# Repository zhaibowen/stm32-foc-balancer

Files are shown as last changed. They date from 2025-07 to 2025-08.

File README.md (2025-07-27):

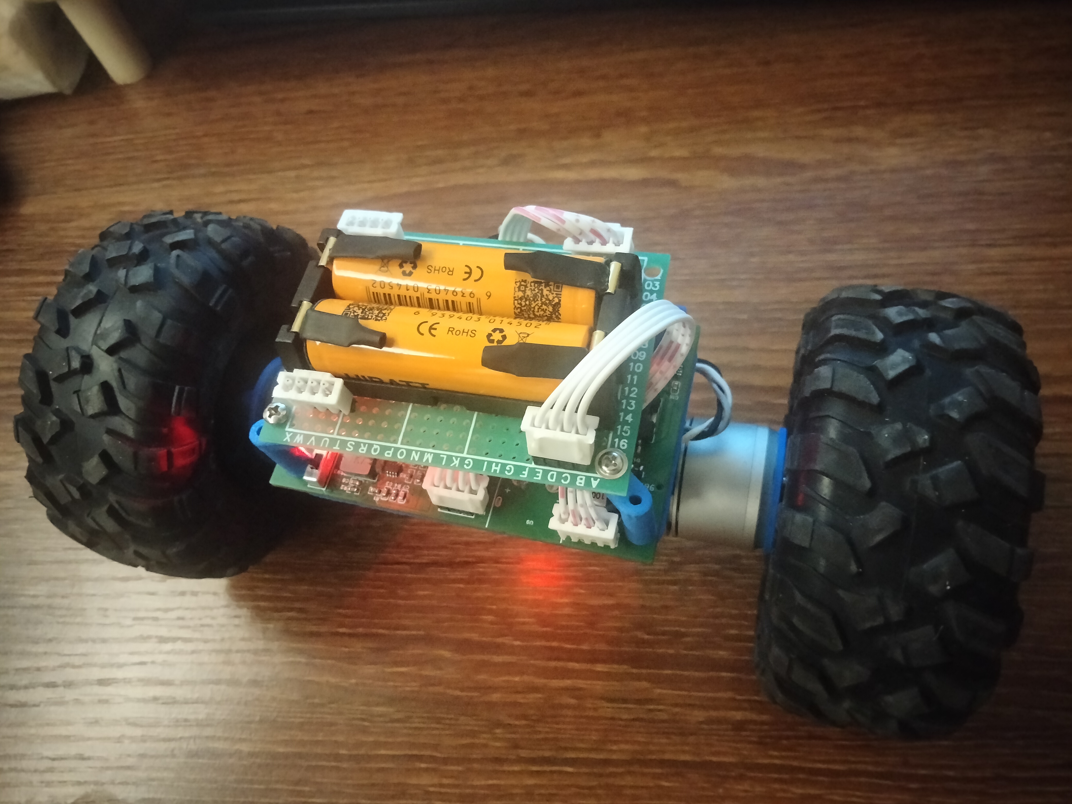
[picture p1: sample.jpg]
示例图片

平衡小车 有感无刷电机2312s  
主控芯片：stm32f103c8t6  
电压模式：频率：833HZ  
&nbsp;&nbsp;&nbsp;&nbsp;&nbsp;&nbsp;&nbsp;&nbsp;&nbsp;&nbsp;&nbsp;&nbsp;&nbsp;&nbsp;&nbsp;&nbsp;&nbsp;&nbsp;FOC控制算法，速度环 + 角度环  
电流模式：频率：666HZ  
&nbsp;&nbsp;&nbsp;&nbsp;&nbsp;&nbsp;&nbsp;&nbsp;&nbsp;&nbsp;&nbsp;&nbsp;&nbsp;&nbsp;&nbsp;&nbsp;&nbsp;&nbsp;FOC控制算法，速度环 + 角度环 + 电流环

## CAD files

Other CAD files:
Fusion360/FOC平衡小车-BLDC-V2 v7.f3d
Fusion360/电机2312s磁编码器d4x2定位架 v1.f3d

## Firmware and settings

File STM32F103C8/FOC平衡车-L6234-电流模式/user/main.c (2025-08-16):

#include "stm32f10x.h"
#include <stdlib.h>
#include "usart.h"
#include "delay.h"
#include "timer.h"
#include "iic.h"
#include "lowpass_filter.h"
#include "pid.h"
#include "foc_utils.h"
#include "BLDCmotor.h" 
#include "MagneticSensor.h"
#include "CurrentSensor.h"
#include "MPU6050.h"
#include "NRF24L01.h"
#include "math.h"

uint8_t Buf[32] = {0};
float max_vel = 20; // rad/s
float max_steering = 0.33; // V
float voltage_supply = 8; // V
float voltage_limit = 2; // V
float current_limit = 4; // A
float pole_pairs = 7;
float i2c_freq = 400000; // Hz

void remote_control_run(float* target_vel, float* target_steering);
void commander_run(uint8_t* debug_flag);

int main(void)
{
	Motor Motor1, Motor2;
	ENCODER_TypeDef Encoder1, Encoder2;
	CurrentSensor CS1, CS2;
	LowPassFilter LPF_M1_vel, LPF_M2_vel;
	LowPassFilter LPF_vel, LPF_pitch, LPF_steering; // 速度，俯仰角，转向
	LowPassFilter LPF_cur1, LPF_cur2;
	PIDController PID_vel, PID_pitch, PID_current;; // 速度，俯仰角，电流
	MPU6050_TypeDef MPU;

	NRF24L01_Init();
	uart_init(115200);
	Motor_init(&Motor1, 1, voltage_supply, voltage_limit, pole_pairs, -1, 6.18, RCC_APB2Periph_GPIOA, GPIOA, GPIO_Pin_11, 1440); // 左轮
	Motor_init(&Motor2, 2, voltage_supply, voltage_limit, pole_pairs, -1, 0.19, RCC_APB2Periph_GPIOA, GPIOA, GPIO_Pin_12, 1440); // 右轮
	TIM2_PWM_Init(Motor1.PWM_Period);
	TIM3_PWM_Init(Motor2.PWM_Period);
	TIM4_10us_Init();
	MagneticSensor_Init(&Encoder1, 1, AS5600_CPR, I2C1);
	MagneticSensor_Init(&Encoder2, 2, AS5600_CPR, I2C2);
	I2C_Init_(I2C1, i2c_freq);
	I2C_Init_(I2C2, i2c_freq);
	MPU6050_Init(&MPU, I2C2);
	printf("MPU ID: %x\r\n", MPU6050_GetID(&MPU));
	delay_ms(1000);            //Wait for the system to stabilize

	Motor_enable(&Motor1);
	Motor_enable(&Motor2);
  	printf("Motor ready.\r\n");

	if (0) {
		MPU6050_CalcGyroOffsets(&MPU);
		alignSensor(&Motor1, &Encoder1);
		alignSensor(&Motor2, &Encoder2);
		Motor_disable(&Motor1);
		Motor_disable(&Motor2);
		return 0;
	}

	CurrentSensor_Init(&CS1, 1, ADC_Channel_3, ADC_Channel_4, -1, 1, 20, 0.012);
	CurrentSensor_Init(&CS2, 2, ADC_Channel_5, ADC_Channel_6, -1, 1, 20, 0.012);

	LowPassFilter_init(&LPF_M1_vel);
	LowPassFilter_init(&LPF_M2_vel);
	LowPassFilter_init(&LPF_pitch);
	LowPassFilter_init(&LPF_vel);
	LowPassFilter_init(&LPF_steering);
	LowPassFilter_init(&LPF_cur1);
	LowPassFilter_init(&LPF_cur2);

	PID_Init(&PID_vel, 0.01, 0, 0, 0, 0.2);
	PID_Init(&PID_pitch, 5, 5, 0, 0, current_limit);
	PID_Init(&PID_current, 2, 4, 0, 0, voltage_limit);

	float target_vel = 0;
	float target_steering = 0;
	float target_M1_volt = 0, target_M2_volt = 0; 
	int pknt = 0;
	unsigned long timestamp_prev = 0;
	uint8_t debug_flag = 0;
	float max_volt = 0;
	int falldown = 0;
	while(1) { // 0.0016s 一个循环
		float shaft_angle_M1 = getAngle(&Encoder1);
		float shaft_angle_M2 = getAngle(&Encoder2);

		float elec_angle_M1 = electricalAngle(&Motor1, shaft_angle_M1);
		float elec_angle_M2 = electricalAngle(&Motor2, shaft_angle_M2);

		MPU6050_Update(&MPU);		//获取MPU6050的数据
		float mpu_pitch = MPU.angleY - 0.07;
		if (fabs(mpu_pitch) > _PI_2) {
			falldown += 1;
			if (falldown > 1000) {
				setPhaseVoltage(&Motor1, 0, elec_angle_M1);
				setPhaseVoltage(&Motor2, 0, elec_angle_M2);
				continue; // 倒地停止
			}
		} else {
			falldown = 0;
		}
		
		float lpf_target_vel = getLowPassFilter(&LPF_vel, target_vel);
		float pid_vel = getPID(&PID_vel, lpf_target_vel - 0);

    	float target_pitch = getLowPassFilter(&LPF_pitch, pid_vel);
		float target_Iq = getPID(&PID_pitch, mpu_pitch - target_pitch);

		getPhaseCurrents(&CS1);
		getPhaseCurrents(&CS2);
		float Iq1 = cal_Iq_Id(CS1.ia, CS1.ib, elec_angle_M1);
		float Iq2 = cal_Iq_Id(CS2.ia, CS2.ib, elec_angle_M2);
		float lpf_Iq1 = getLowPassFilter(&LPF_cur1, Iq1);
		float lpf_Iq2 = getLowPassFilter(&LPF_cur2, Iq2);
		float Iq_avg = (-lpf_Iq1 + lpf_Iq2) / 2.0; // 反向
		float voltage_control = getPID(&PID_current, target_Iq - Iq_avg);

		float steering_adj = getLowPassFilter(&LPF_steering, target_steering);	
		target_M1_volt = _constrain(voltage_control - steering_adj, -voltage_limit, voltage_limit);
		target_M2_volt = _constrain(-voltage_control - steering_adj, -voltage_limit, voltage_limit);
		
  		setPhaseVoltage(&Motor1, target_M1_volt, elec_angle_M1);
  		setPhaseVoltage(&Motor2, target_M2_volt, elec_angle_M2);

		max_volt = fmax(max_volt, fabs(voltage_control));
		if (debug_flag) {
			unsigned long now_us;
			float Ts;
			now_us = time_cntr;
			if (now_us < timestamp_prev) {
				Ts = (ulong_max_value - timestamp_prev + now_us) * 1e-5;
			} else {
				Ts = (now_us - timestamp_prev) * 1e-5;
			}
			timestamp_prev = now_us;

			if (pknt == 0) {
				// printf("%.5f, %.4f, %.4f, %.4f, %.4f, %.4f, %.4f, %.4f, %.4f, %.4f,\t %.4f, %.4f, %.4f, %.4f\r\n", 
				// 	Ts, target_vel, lpf_target_vel, target_steering, steering_adj, mpu_pitch, MPU.gyroY, MPU.angleAccY, pid_vel, target_pitch, 
				// 	voltage_control, target_M1_volt, -target_M2_volt, max_volt);
				printf("%.5f, %.4f, %.4f, %.4f, %.4f, %.4f,\t %.4f, %.4f, %.4f, %.4f, %.4f, %.4f, %.4f, %.4f, %.4f, %.4f\r\n", 
					Ts, target_vel, lpf_target_vel, target_steering, steering_adj, mpu_pitch,
					CS1.ia, CS1.ib, Iq1, lpf_Iq1, CS2.ia, CS2.ib, Iq2, lpf_Iq2, Iq_avg, target_Iq);
				max_volt = 0;
				pknt = 100;
			}
			pknt -= 1;
		}
		remote_control_run(&target_vel, &target_steering);
		commander_run(&debug_flag);
	}
}

void remote_control_run(float* target_vel, float* target_steering) {
	uint16_t X, Y;
	if (NRF24L01_Get_Value_Flag() == 0) {
		NRF24L01_GetRxBuf(Buf);
		X = Buf[1] * 256 + Buf[0];
		Y = Buf[3] * 256 + Buf[2];
		if (Y < 2500 && Y > 1500) Y = 2048;
		if (Y != 2048) { // 前进和转向分开
			if (X < 2500 && X > 1500) X = 2048;
		}
		*target_vel = -(Y - 2048) / 2048.0 * max_vel;
		*target_steering = -(X - 2048) / 2048.0 * max_steering;
	}
}

void commander_run(uint8_t* debug_flag) {
	if((USART_RX_STA&0x8000) != 0)
	{
		switch(USART_RX_BUF[0])
		{
			case 'D': // debug
				*debug_flag = atoi((const char *)(USART_RX_BUF+1));
				printf("debug_flag=%d\r\n", *debug_flag);
				break;
		}
		USART_RX_STA=0;
	}
}

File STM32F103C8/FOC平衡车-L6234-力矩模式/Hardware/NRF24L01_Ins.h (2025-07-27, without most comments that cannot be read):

#ifndef __nRF24L01_H
#define __nRF24L01_H


#define IRQ_Port	GPIOA
#define CE_Port		GPIOB
#define CSN_Port	GPIOB
#define SCK_Port	GPIOB
#define MOSI_Port	GPIOB
#define MISO_Port	GPIOB

#define IRQ_Pin		GPIO_Pin_8
#define CE_Pin		GPIO_Pin_5
#define CSN_Pin		GPIO_Pin_12
#define SCK_Pin		GPIO_Pin_13
#define MOSI_Pin	GPIO_Pin_14
#define MISO_Pin	GPIO_Pin_15


#define nRF_READ_REG        0x00 
#define nRF_WRITE_REG       0x20 
#define RD_RX_PLOAD     0x61  
#define WR_TX_PLOAD     0xA0  
#define FLUSH_TX        0xE1  
#define FLUSH_RX        0xE2  
#define REUSE_TX_PL     0xE3  
#define NOP             0xFF  

#define CONFIG          0x00                           
#define EN_AA           0x01  
#define EN_RXADDR       0x02  
#define SETUP_AW        0x03  
#define SETUP_RETR      0x04  
#define RF_CH           0x05  
#define RF_SETUP        0x06  
#define STATUS          0x07  
#define OBSERVE_TX      0x08  
#define CD              0x09  
#define RX_ADDR_P0      0x0A  
#define RX_ADDR_P1      0x0B  
#define RX_ADDR_P2      0x0C  
#define RX_ADDR_P3      0x0D  
#define RX_ADDR_P4      0x0E  
#define RX_ADDR_P5      0x0F  
#define TX_ADDR         0x10  
#define RX_PW_P0        0x11   
#define RX_PW_P1        0x12   
#define RX_PW_P2        0x13   
#define RX_PW_P3        0x14   
#define RX_PW_P4        0x15  
#define RX_PW_P5        0x16  
#define FIFO_STATUS     0x17  


#define MAX_TX  	0x10
#define TX_OK   	0x20
#define RX_OK   	0x40

#endif
